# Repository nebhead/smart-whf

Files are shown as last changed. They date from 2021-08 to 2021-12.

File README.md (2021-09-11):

# Smart Whole House Fan

## ESP8266 Based Whole House Fan Controller / Timer

This is a _smarter_ whole house fan controller that can be controlled via a Web UI, and sports a nice OLED screen for status while operating.

**Warning:** It should not go without saying that working with high voltage power is extremely dangerous and should be attempted only by experienced/qualified persons.  This project is provided as-is, with no warranty, gaurentees of fitness, and disclaims all potential damages.  The developer assumes no liability for damage, injury or death that might result from using this.  Implement at your own risk.  

__Features:__

* Web UI for controlling speed and setting timer
* OLED Screen displays operation and timer
* Physical buttons to adjust speed and timer
* Physical button LOCK to prevent kids, accidental or curious button pushers from starting up the fan when you don't want them to
* REST API for controlling the fan via an application (no API key)
* MQTT support for Home Assistant (this needs some help, but the basics work)
* 3D Printable Faceplates / Buttons for mounting

__Pictures:__

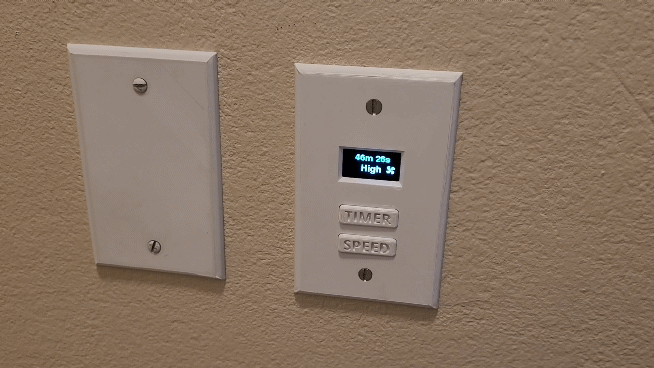
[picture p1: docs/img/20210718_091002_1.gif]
The Finished Product

The final product.  

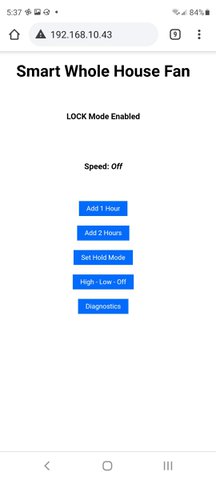
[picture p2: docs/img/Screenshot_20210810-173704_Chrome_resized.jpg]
Chrome

Chrome Screenshot on a mobile device.

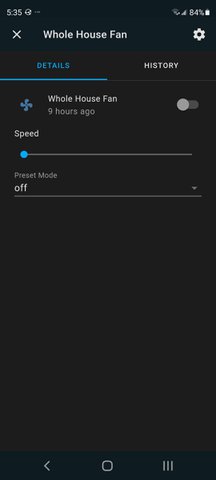
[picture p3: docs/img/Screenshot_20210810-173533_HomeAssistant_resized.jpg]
Home Assistant

Home Assistant Screenshot on a mobile device.

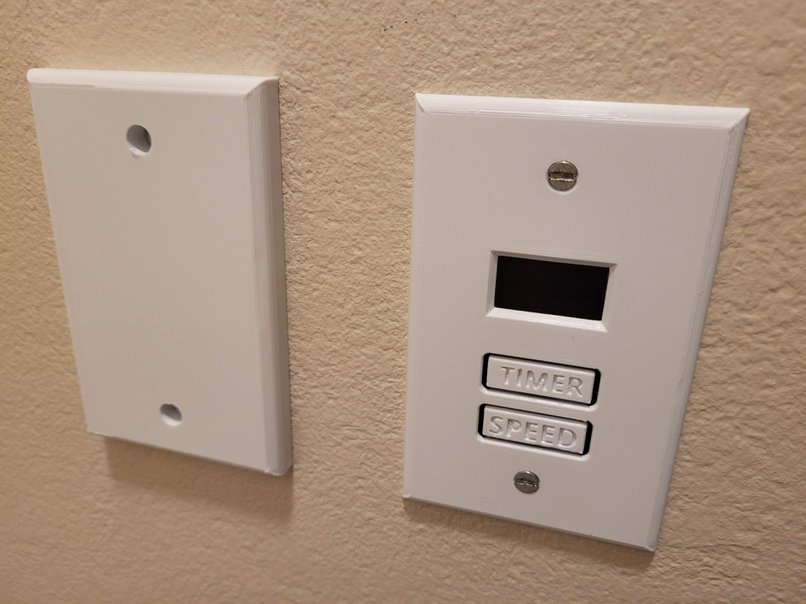
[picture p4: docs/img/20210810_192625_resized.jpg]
Off State

This is the final 3D Printed design with integrated buttons on the control side and a thicker wall plate on the relay side (for more space).

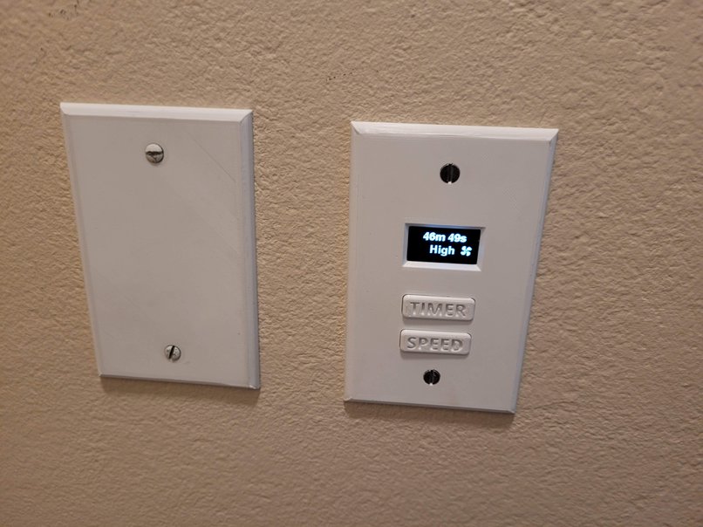
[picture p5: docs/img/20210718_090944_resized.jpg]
On State

This is the original 3D printed design, with large free-floating buttons.  But this give you a better idea of what the display looks like. 

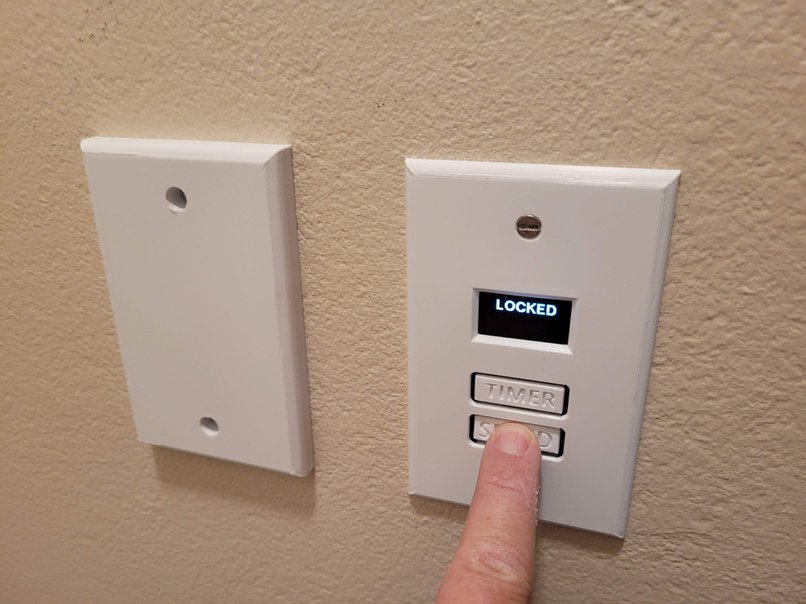
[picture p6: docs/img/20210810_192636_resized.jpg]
LOCKED

Example of what happens when the physical buttons are locked out and someone presses a button.  

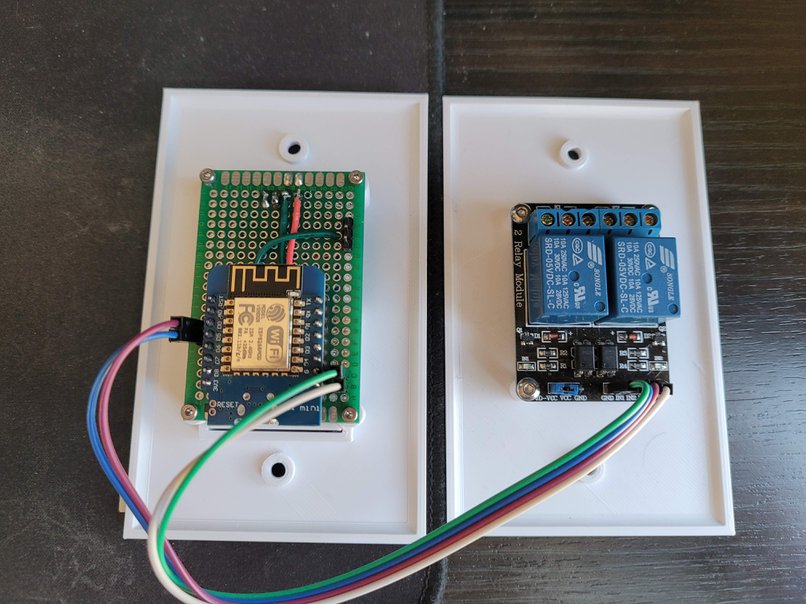
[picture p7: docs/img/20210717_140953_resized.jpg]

An example of how I mounted the perfboard to the backside of the outlet faceplate.  Also the relay mounted to the back of the faceplate.  In retrospect, it might be good to mount the relay up higher so that it has space for the wiring coming out of the bottom.  

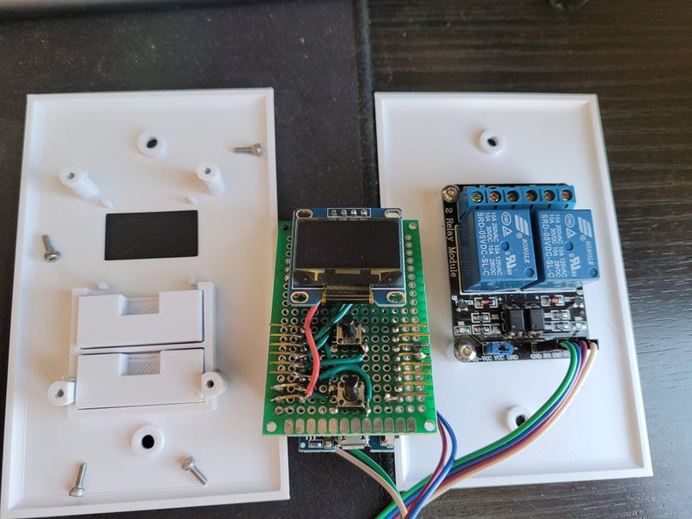
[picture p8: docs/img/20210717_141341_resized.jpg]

Front side of the perfboard wiring, with tack switches, and OLED display.  Note I used some taller tack switches, but you could modify the buttons ont he 3D print to go lower if you want.  

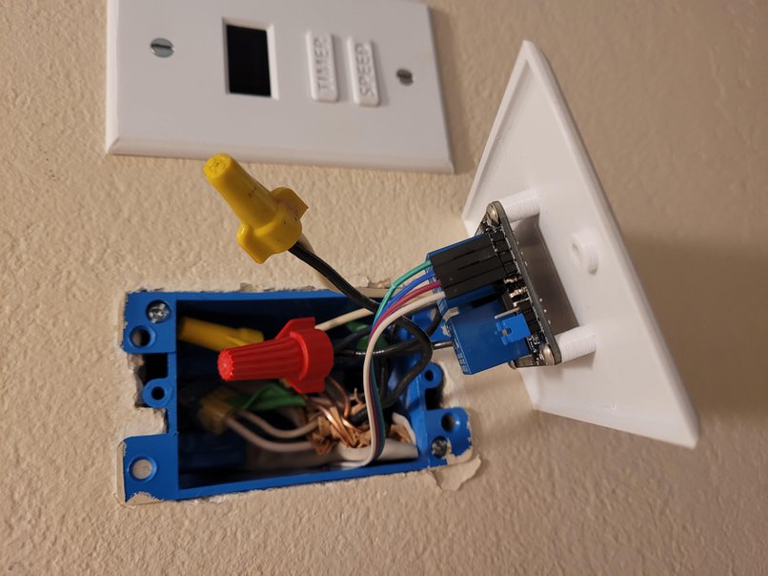
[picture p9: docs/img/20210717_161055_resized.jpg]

AHhh! Not enough space for the relay to tuck up into this outlet.  I ended up switching to smaller wire nuts and 18 AWG wire for the connections to the relay AND thickened the 3D printed wall plate so that it could all fit.  

### The Parts List

* **ESP8266 Board** - I used a Wemos D1 Mini due to it's small form factor, but many other variants of ESP8266 boards could be used as well.  I ordered [these D1 Mini boards](https://www.amazon.com/gp/product/B081PX9YFV) from Amazon, which are great because they come with lots of header options that you can choose from.  This made it easy for me to use a longer pin female headers to stick through the perfboard and to use to make connections to the other components.   
* **2-Channel Relay** - Used to control power to High / Low speeds. Using the mechanical relays, as they seem to have a higher current rating.  [Amazon Link](https://www.amazon.com/SainSmart-101-70-100-2-Channel-Relay-Module/dp/B0057OC6D8)
* **120V AC Power Supply to 5V DC** - Got this incredibly tiny supply from Amazon that can fit in the enclosure.  It's amazing.  [Amazon Link](https://www.amazon.com/gp/product/B08ZSW2PP8)
* **Dupont Cables** - Female to Female for connecting your GPIOs to the relay board. Readily found on Amazon, etc.  
* **SSD1306 OLED Display** - Cheap and commonly found OLED display. This is not the specific one I used, but here is a similar verson on [Amazon](https://www.amazon.com/128X64-Display-SSD1306-Arduino-Raspberry/dp/B085WCRS7C). 
* **Tactile Switches** - I purchased a bunch of sizes of tactile switches and just used the 8 or 9mm sizes for my project, but your mileage may vary. [Amazon Link](https://www.amazon.com/gp/product/B071KX71SV)
* **Project Board** - I utilized some standard 4cm x 6cm project board for this project, but you could choose to utilize other sizes.  [Amazon Link](https://www.amazon.com/gp/product/B00NQ37V0K)
* **2.54pitch headers** - As with the dupont cables, these can be readily found almost anywhere, including Amazon.
* **220V 5A Slow Blow Fuses & Fuse Holders** - To add some protection to your home, I highly recommend using a fuse to this build so that if a short occurs, it will hopefully blow the fuse and prevent an electrical fire.  [Amazon Link to Fuse Assortment](https://www.amazon.com/gp/product/B08QCDHPCJ/),  [Amazon Link to Fuse Holder](https://www.amazon.com/DIGITEN-5x20mm-Holder-Inline-screw/dp/B00VLBAF84/)

### Default GPIO Mapping
+ GPIO 0 - Add Time Button
+ GPIO 2 - Cycle Speed Button (High, Low, Off)
+ GPIO 14 - Relay for HIGH speed
+ GPIO 16 - Relay for LOW speed 

### Schematics

Basic Wiring Schematic for the entire project.  This was built for my home system and yours may vary.  Please build this at your own risk.  The developer takes no responsibility for destroyed equipment, house fires, electric shock.  Please do not attempt unless you are confident you know what you are doing.  

__Low Voltage Schematic:__
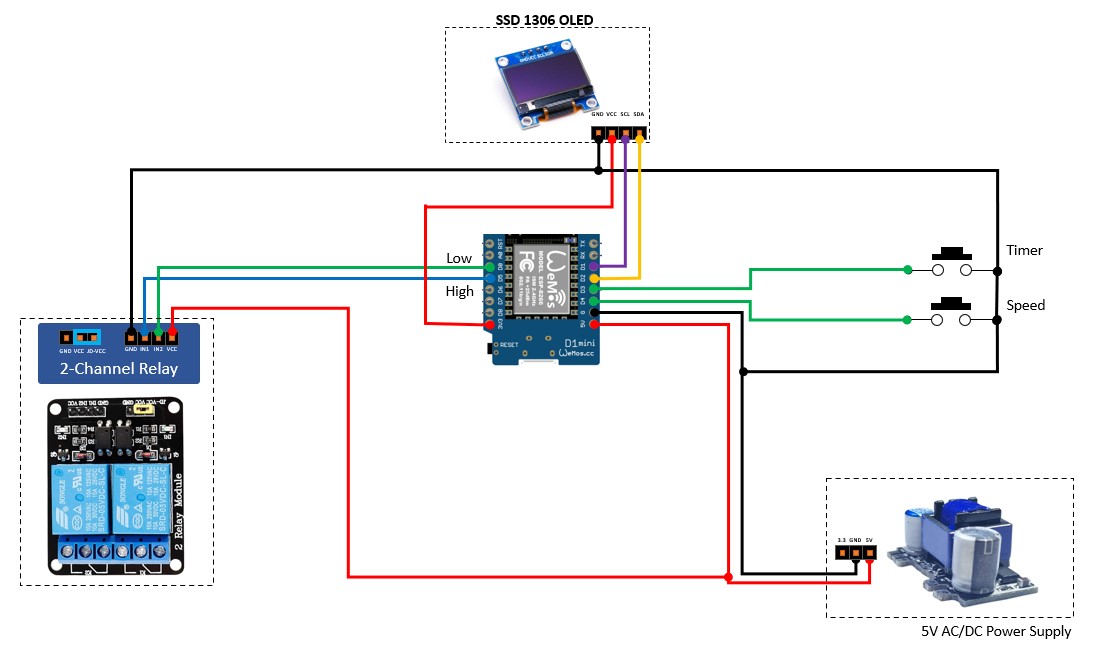
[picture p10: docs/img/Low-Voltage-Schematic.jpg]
Low Voltage Schematic


__High Voltage Schematic:__
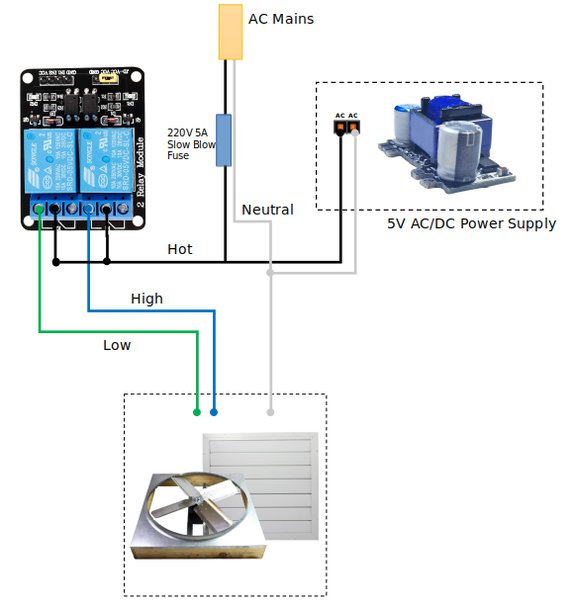
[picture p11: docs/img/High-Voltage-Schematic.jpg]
High Voltage Schematic


### HW Install

Standard whole house fan systems generally have two speeds that are selected by applying power to either the high speed circuit or the low speed circuit.  In the reference schematic above, we show that the relays are acting as the selector for the hot (black) wire, feeding AC current to the fan.  The nuetral should be wired together with a wirenut (or other terminal).  

I personally ended up using 18 guage wire for the connections to the relay due to the challenges of the tight space in my wall box.  However, you may want to check the wiring requirements for your whole house fan, to ensure you are using the minimum gauge wire.  

Also the power supply that I selected, simply needs mains hot and nuetral connected.  On this side, I used 18 gauge wire, simply because this is what I had, and it should be safe give the small amount of power this supply is using.  

## Software Installation

 ##### To install the ESP8266 board, (using Arduino 1.6.4+):
  - Add the following 3rd party board manager under "File -> Preferences -> Additional Boards Manager URLs":
       http://arduino.esp8266.com/stable/package_esp8266com_index.json
  - Open the "Tools -> Board -> Board Manager" and click install for the ESP8266"
  - Select your ESP8266 in "Tools -> Board"

 ##### Library Dependancies include:
   - WiFiManager (by TZAPU) (https://github.com/tzapu/WiFiManager)
   - Adafruit SSD1306 for the OLED display
   - Adafruit GFX library for graphics manipulations / fonts 
   - ArduinoJSON for parsing API inputs / outputs
   - PubSubClient for MQTT Capabilities

  To install the libraries, go to the libraries manager in the Arduino IDE (Tools -> Manage Libraries).  Search for the libraries listed above and install each.  

 ##### MQTT Settings

  Make sure that the following line in smart-whf.ino is not commented out:

  ```
  #define mqttenabled // Comment out this line to disable MQTT support
  ```
  
  In the smart-whf.ino file, modify your MQTT settings for your setup, if using the MQTT feature.  The WifiManager has all of these settings included, however, if you can pre-populate these, it makes setup just a little faster.  

```  
// Edit these values for your implementation
char defaultmqttServer[] = "192.168.10.46";  // put your MQTT Server Address here
char defaultmqttPort[] = "1883"; // put your MQTT Server Port here
char defaultmqttUser[] = "mqtt-user"; // put your MQTT Server Username here
char defaultmqttPassword[] = "password"; // put your MQTT Server Password here
// End value edit
```

 ##### Configure Home Assistant

   First you'll need to ensure that MQTT Broker has been installed from the add-on store.  This is out of scope of this guide, but it's likley that you already have this installed if you are reading this.  Then, modify the `configuration.yaml` file by adding the below:

```
# Configuration for the whole house fan in Home Assistant
# The below goes into your configuration.yaml file

fan whft:
- platform: mqtt
  name: "Whole House Fan"
  icon: "mdi:fan"
  state_topic: "whfan/on/state"
  command_topic: "whfan/on/set"
  percentage_state_topic: "whfan/percentage/state"
  percentage_command_topic: "whfan/percentage/set"
  preset_mode_command_topic: "whfan/preset/set"
  preset_mode_state_topic: "whfan/preset/state"
  preset_modes:
  - "timer"
  - "hold"
  - "off"
  payload_on: "ON"
  payload_off: "OFF"
  speed_range_min: 1
  speed_range_max: 2
  qos: 0  
```

Restart Home Assistant and you should be able to add the Smart Whole House Fan entity to your UI.  

__NOTE:__ I could _really_ use some help from anyone who has experience with Home Assistant to improve this configuration and MQTT support.  For example, being able to add time to the timer from the Home Assistant UI would be awesome.  This is an area I just haven't had time to mess with. 

 ##### Initial Wifi Setup: 
  - To connect your device to WiFi, use a smartphone or computer with WiFi to connect to the board AP (SSID: Smart-WHF-AP).
  - Then open a broswer and navigate to __192.168.4.1__ to configure the device for WiFi.
  - Optionally configure MQTT settings, if you have it built in.  
  - Once configured for your wifi network, you should be all set. 

 ### 3D Printed Parts

 You'll find STL's for 3D Printing your own faceplates in the `/assets/stl/` folder.  

 All STL files were created using OnShape which is free for personal use.  The original design files are located [here](https://cad.onshape.com/documents/4ed1076b86430447dbe85914/w/bb85ae4fb526a0970ad92e38/e/43ed86bf169133e95db9fccc) so that you can copy, export, and make your own tweaks to fit your needs.  

 There are a few options to choose from.  

- __Two single-gang outlet boxes:__ 
  * __Control-Face-Plate.stl:__ Standard Control Face Plate, without buttons.  In this configuration, you'll need to print the __SpeedButtonTall.stl__ and the __TimeButton-Tall.stl__ which can be assembled later.  I found this version to be a little finicky with button presses, but your mileage may vary.  All should print in place with no supports. 
  * __Control-Face-Plate-Int-Buttons.stl:__ This is the same Control Face Plate as above, but with integrated buttons.  This should print in place, with no supports.  I found this version to be much more reliable with button presses, giving a satisfying click on each button press.  It's not as aesthetically pleasing as the above, but it is more functional.
  * __Relay-Face-Plate.stl:__ Standard thickness faceplate for mounting the relay module to.  Prints in place with no supports.  
  * __Relay-Face-Thicc.stl:__ A thicker relay face plate to accomodate space for the relay module and the bulk of wiring inside the outlet box.  I eventually settled on this solution due to the amount of wiring in my installation.  Prints in place with no supports. 

- __One dual-gang outlet box:__
  * __Dual-Gang-Face-Full.stl:__ This is a single faceplate with mounting for both the relay module and the control board w/OLED screen.  Buttons are integrated, as I feel this is a much better button solution.  

- __Power Supply Box (optional):__
  * __PowerSupplyBase - PSBase.stl:__ This is the optional base for the above linked power supply.  I wanted to enclose the power-supply to ensure that there were no shorts if any of the mains wires (or ground) was accidentally touching.  Print in place, no supports. 
  * __PowerSupplyLid - PSLid.stl:__ The lid for the power-supply box.  Print in place, no supports. 

Mounting hardware for the boards are simple M3x8mm (or M3x5mm) bolts.  

### Usage

There are effectively four different ways to use the Smart Whole House fan.  

__1. Physical Buttons__

The physical buttons on the front are fairly simple to use.  

The "Timer" button will set the timer in the following increments when pressed: 1h, 2h, 3h, 4h, 6h, 8h, 10h, HOLD (hold will keep the fan on indefinitely).  

The "Speed" button will cycle through speed settings when pressed: High -> Low -> Off

Pressing the Speed button when the fan is OFF, will set the timer to the default time of 1h automatically.  However, pressing the Timer button when the fan is off, will not select the speed.  

Pressing the Speed button and the Timer button at the _same_ time will briefly display the WiFi SSID and the IP Address of the device.  This might be helpful if you are trying to connect to the web interface and forgot the IP.  

Pressing the Speed button and the Timer button at the _same_ time for six seconds will __LOCK__ the physical buttons.  If the buttons are pressed after LOCK mode is enabled, then the screen will display "LOCKED".  Pressing the Speed button and the Timer button at the _same_ time for three more seconds will __UNLOCK__ the physical buttons.  __Note:__ Locking from the physical buttons will cancel the timer and turn off the fan, if it was already running.  Turning on the fan from the WebUI, MQTT, or API will disable lock mode as a safety mechanism, so you always have the ability to turn off from physical buttons while the fan is running. 

__2. WebUI__

The WebUI can be accessed from any browser by going to the IP address of the device.  There is a menu of buttons, similar to the physical buttons, but slightly different.  

* __Add 1 Hour__ - This allows you to add an hour to the timer. 
* __Add 2 Hours__ - This allows you to add two hours to the timer.
* __Set Hold Mode__ - This will enter hold mode, and the fan will be active until turned off. 
* __High - Low - Off__ - Similar to the physical button for speed, this will cycle through High -> Low -> Off modes.  
* __Diagnositcs__ - This will take you to some additional information about the WiFi Network, MQTT Status, and will allow you to __RESTART__ the device, or to __LOCK/UNLOCK__ the physical buttons.  

__3. MQTT w/HomeAssistant__

As described in the Home Assistant section above, the MQTT interface can be used to control the fan.  This means that the whole house fan can even be controlled via your Google Home or Amazon Alexa enabled devices.  The interface in Home Assistant is pretty basic (on/off), set fan speed low/high/off, and set the preset mode to timer/hold/off.  Admittedly, this is my first project using MQTT and Home Assistant, so feedback on how to improve this is very welcome.  

__4. REST API__

Last but not least, there is a basic REST API that can be utilized to control the fan functions as well.  

A GET request to http://whf.device.ip.address/api will return the following if the fan is off: 

```
{"power":"off","speed":"off"}
```

If the fan is running, it will return something like this: 

```
{"power":"on","speed":"low","holdmode":false,"timer":"59m 46s"}
```

A POST request to http://whf.device.ip.address/api should contain commands in the following JSON format: 

```
    {
      "power" : "on", "off"           # Turn on or off
      "speed" : "high", "low", "off"  # Can be high, low or off
      "holdmode" : True, False        # Can be True or False
      "addtime" : 1,2                 # Add hours can be 1 or 2
    }
```

On a POST request, the fan will return the same JSON output as above if running or off.  

### Credits

Created by Ben Parmeter. Check out my other projects on [github](https://github.com/nebhead). If you enjoy this software and feel the need to donate a cup of coffee, a frosty beer or a bottle of wine to the developer you can click [here](https://paypal.me/benparmeter).

Of course, none of this project would be available without the wonderful and amazing folks below.  If I forgot anyone please don't hesitate to let me know.  

* **Adafruit** - for the SSD1306 and Graphics Libraries.  
* **WiFiManager** - by TZAPU [github](https://github.com/tzapu/WiFiManager)
* **ArduinoJSON** - by Benoît Blanchon for making parsing inputs/outputs of the API easier [arduinojson.org](https://arduinojson.org/)
* **PubSubClient** - by Nick O'Leary for adding the MQTT capabilities to the fan [github.com](https://github.com/knolleary/pubsubclient)

### Licensing

This project is licensed under the MIT license.

```
MIT License

Copyright (c) 2021 Ben Parmeter

Permission is hereby granted, free of charge, to any person obtaining a copy
of this software and associated documentation files (the "Software"), to deal
in the Software without restriction, including without limitation the rights
to use, copy, modify, merge, publish, distribute, sublicense, and/or sell
copies of the Software, and to permit persons to whom the Software is
furnished to do so, subject to the following conditions:

The above copyright notice and this permission notice shall be included in all
copies or substantial portions of the Software.

THE SOFTWARE IS PROVIDED "AS IS", WITHOUT WARRANTY OF ANY KIND, EXPRESS OR
IMPLIED, INCLUDING BUT NOT LIMITED TO THE WARRANTIES OF MERCHANTABILITY,
FITNESS FOR A PARTICULAR PURPOSE AND NONINFRINGEMENT. IN NO EVENT SHALL THE
AUTHORS OR COPYRIGHT HOLDERS BE LIABLE FOR ANY CLAIM, DAMAGES OR OTHER
LIABILITY, WHETHER IN AN ACTION OF CONTRACT, TORT OR OTHERWISE, ARISING FROM,
OUT OF OR IN CONNECTION WITH THE SOFTWARE OR THE USE OR OTHER DEALINGS IN THE
SOFTWARE.
```

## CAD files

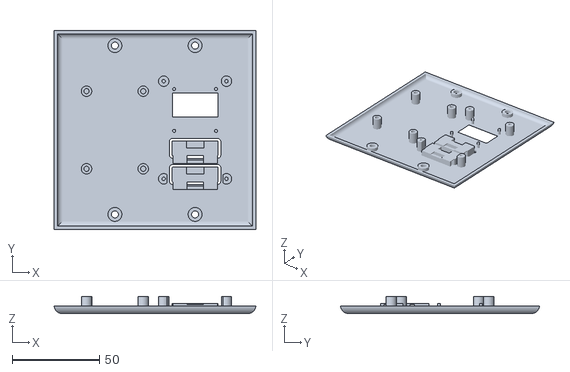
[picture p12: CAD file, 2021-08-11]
assets/stl/Dual-Gang-Face-Full.stl
115.8 x 114.2 x 10.0

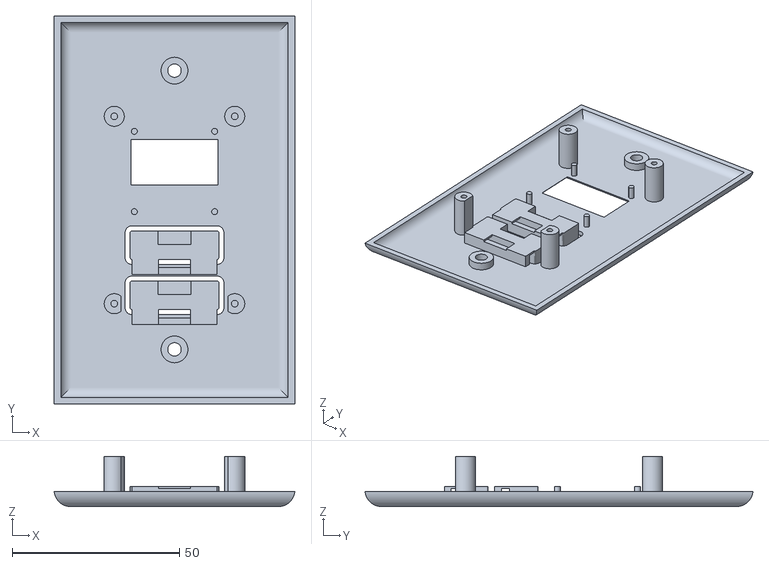
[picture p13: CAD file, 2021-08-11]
assets/stl/Control-Face-Plate-Int-Buttons.stl
71.9 x 115.9 x 15.0

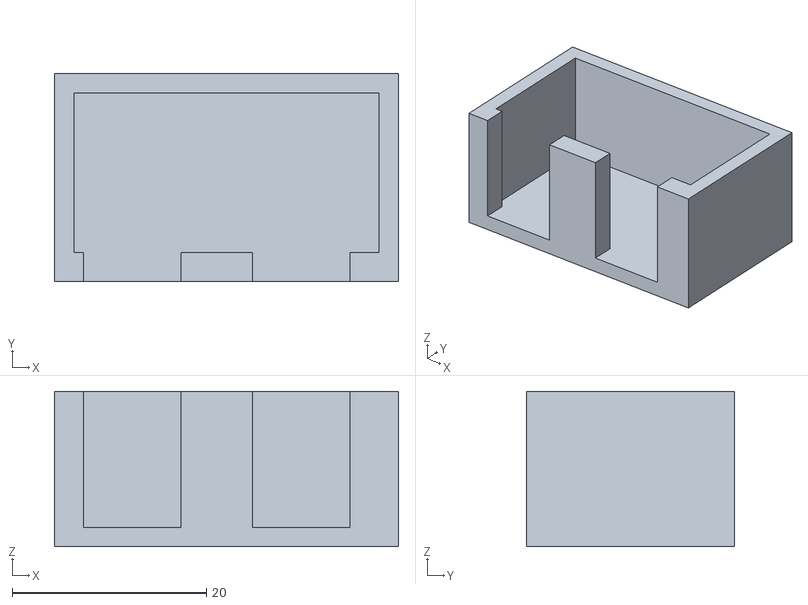
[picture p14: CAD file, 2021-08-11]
assets/stl/PowerSupplyBase - PSBase.stl
35.4 x 21.4 x 16.0

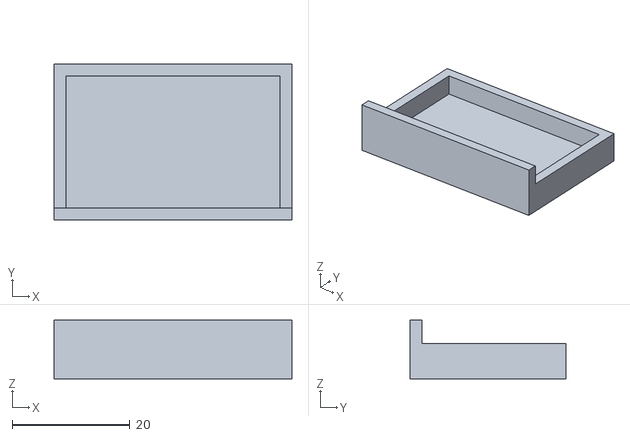
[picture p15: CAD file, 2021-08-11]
assets/stl/PowerSupplyLid - PSLid.stl
40.4 x 26.4 x 10.0

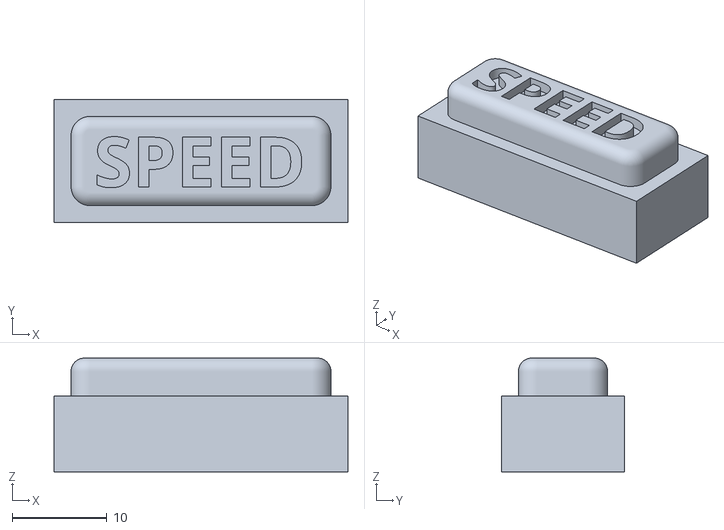
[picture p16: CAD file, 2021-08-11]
assets/stl/SpeedButtonTall.stl
31.0 x 13.0 x 12.0

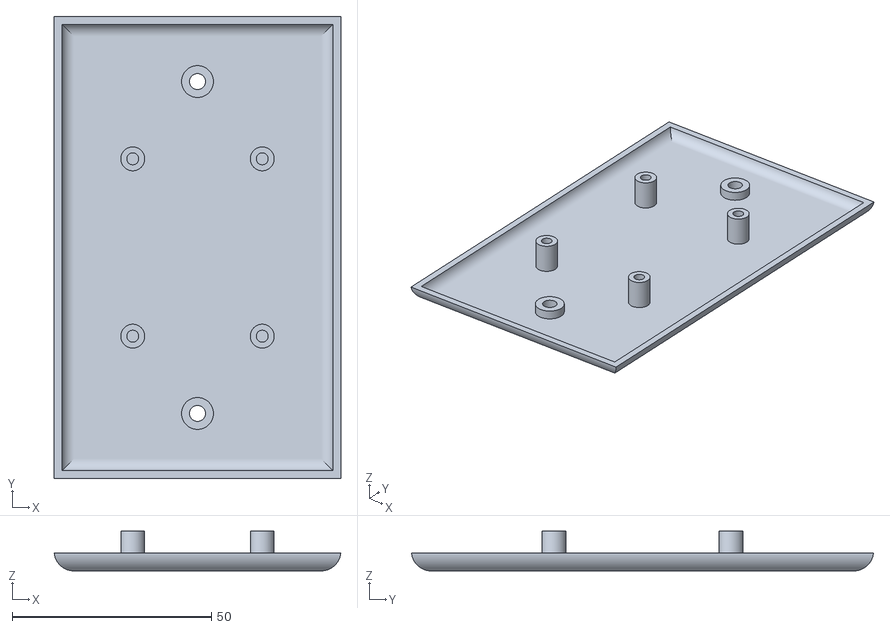
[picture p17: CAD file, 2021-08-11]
assets/stl/Relay-Face-Plate.stl
71.9 x 115.9 x 10.0

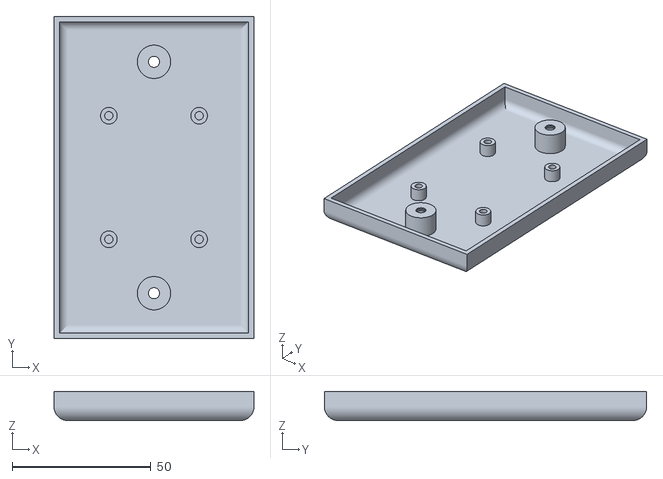
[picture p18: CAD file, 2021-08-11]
assets/stl/Relay-Face-Thicc.stl
72.0 x 116.0 x 10.5

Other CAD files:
assets/stl/TimeButton-Tall.stl
assets/stl/Control-Face-Plate.stl

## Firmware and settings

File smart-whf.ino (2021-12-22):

/*
 Simple Smart Whole House Fan Timer Controller

 Controlled via physical buttons or web user interface. 

 Designed for ESP8266 based boards like the Wemos D1 Mini or NodeMCU
 
 To install the ESP8266 board, (using Arduino 1.6.4+):
  - Add the following 3rd party board manager under "File -> Preferences -> Additional Boards Manager URLs":
       http://arduino.esp8266.com/stable/package_esp8266com_index.json
  - Open the "Tools -> Board -> Board Manager" and click install for the ESP8266"
  - Select your ESP8266 in "Tools -> Board"

 Dependancies include:
   - WiFiManager (by TZAPU) (https://github.com/tzapu/WiFiManager)
   - Adafruit SSD1306 for the OLED display
   - Adafruit GFX library for graphics manipulations / fonts 
   - ArduinoJSON for parsing API inputs / outputs
   - PubSubClient for MQTT Capabilities

 Initial Wifi Setup: 
  To connect your device to WiFi, use a smartphone or computer with WiFi to connect to the board AP (SSID: Smart-WHF-AP).
  Then open a broswer and navigate to 192.168.4.1 to configure the device for WiFi. 
*/

#define mqttenabled // Comment out this line to disable MQTT support
#include <FS.h> // Apparently need this to be included first
#include <ESP8266WiFi.h>
#include <WiFiClient.h>
#include <ESP8266mDNS.h>
#include <ESP8266WebServer.h>   // Include the WebServer library
#include <WiFiManager.h> 
#include <SPI.h>
#include <Wire.h>
#include <Adafruit_GFX.h>
#include <Adafruit_SSD1306.h>
#include <Fonts/FreeSansBold12pt7b.h>
#include <ArduinoJson.h>
#include <WiFiUdp.h>
#include <ArduinoOTA.h>

#ifdef mqttenabled
// If MQTT enabled, then setup mqtt
#include <PubSubClient.h>

// Edit these values for your implementation
char defaultmqttServer[] = "192.168.10.242";  // put your MQTT Server Address here
char defaultmqttPort[] = "1883"; // put your MQTT Server Port here
char defaultmqttUser[] = "mqtt-user"; // put your MQTT Server Username here
char defaultmqttPassword[] = "password"; // put your MQTT Server Password here
int mqttRetries = 100; // number of retries before disabling MQTT, if connection fails
// End value edit
String mqttServer = String(defaultmqttServer);
int mqttPort = atoi(defaultmqttPort);
String mqttUser = String(defaultmqttUser);
String mqttPassword = String(defaultmqttPassword);
const char* mqttCommandTopic = "whfan/on/set";
const char* mqttPresetCommandTopic = "whfan/preset/set";
const char* mqttPresetStateTopic = "whfan/preset/state";
const char* mqttStateTopic = "whfan/on/state";
const char* mqttAvailTopic = "whfan/on/avail";
const char* mqttSpeedStateTopic = "whfan/speed/state";
const char* mqttSpeedCommandTopic = "whfan/speed/set";
const char* mqttPercentageStateTopic = "whfan/percentage/state";
const char* mqttPercentageCommandTopic = "whfan/percentage/set";
unsigned long mqttLastCheck; 
WiFiClient espClient;
PubSubClient client(espClient);
#endif 

const char* wifiHostname = "whfan";
ESP8266WebServer server(80);    // Create a webserver object that listens for HTTP request on port 80

#define SCREEN_WIDTH 128 // OLED display width, in pixels
#define SCREEN_HEIGHT 64 // OLED display height, in pixels

// Declaration for an SSD1306 display connected to I2C (SDA, SCL pins)
// The pins for I2C are defined by the Wire-library. 
// On an arduino UNO:       A4(SDA), A5(SCL)
// On an arduino MEGA 2560: 20(SDA), 21(SCL)
// On an arduino LEONARDO:   2(SDA),  3(SCL), ...
#define OLED_RESET     -1 // Reset pin # (or -1 if sharing Arduino reset pin)
#define SCREEN_ADDRESS 0x3C ///< See datasheet for Address; 0x3D for 128x64, 0x3C for 128x32
Adafruit_SSD1306 display(SCREEN_WIDTH, SCREEN_HEIGHT, &Wire, OLED_RESET);

#define DEBOUNCE 250 // Millisecond debounce for buttons
#define REFRESH 200 // Millisecond refresh for display 
#define GPIO_timebtn 0 // Input button for time selection
#define GPIO_speedbtn 2 // Input button for speed selection
#define GPIO_HIGHrelay 14 // High Fan Speed Relay Output Enable
#define GPIO_LOWrelay 16 // Low Fan Speed Relay Output Enable

int state = 0;  // Current Fan Speed / State : 0 = Off, 1 = High, 2 = Low
int iconstate = 0;  // Current Icon Animation Image : 0 = Starting Position, 1-2 = 22.5d rotated, 3-4 = 45d rotated, 5-6 = 67.5d rotated
bool holdmode = false; // Indicates hold mode
bool lockmode = false; // Indicates lock mode (physical buttons are locked)
bool lockinitiated = false;  // Indicates unlock / lock mode has been initiated
unsigned long locktimer = 0; // Tracks start time of lock / unlock events
unsigned long start_time = 0;   // Track start time of the fan
unsigned long runtime = 0;  // Track total runtime
unsigned long timebtnlastpress = 0;  // Millis when the time button was last pressed, for debounce
unsigned long spdbtnlastpress = 0;  // Millis when the speed button was last pressed, for debounce
unsigned long displayrefreshlast = 0;  // Millis when the screen was last refreshed
unsigned long now = 0; // Tracks the current millis output

String timestring = "";  // Time String to display

String favicon = "<link rel=\"shortcut icon\" href=\"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" />";

// Fan Icon Animation - 24x24 ICON rotates 22.5 degrees per step
const unsigned char fanicon0 [] PROGMEM = {
  0x00, 0x3e, 0x00, 0x00, 0x7f, 0x80, 0x00, 0xff, 0x80, 0x00, 0xff, 0x80, 0x00, 0xff, 0x80, 0x00, 
  0xff, 0x00, 0x00, 0x7e, 0x00, 0x78, 0x7c, 0x00, 0x7c, 0x3c, 0x38, 0xfe, 0x66, 0xfe, 0xff, 0xd3, 
  0xfe, 0xff, 0xb9, 0xff, 0xff, 0x99, 0xff, 0xff, 0xc3, 0xff, 0x7f, 0x64, 0x7f, 0x1c, 0x3c, 0x3e, 
  0x00, 0x3e, 0x1e, 0x00, 0x7e, 0x00, 0x00, 0xff, 0x00, 0x01, 0xff, 0x00, 0x01, 0xff, 0x00, 0x01, 
  0xfe, 0x00, 0x01, 0xfe, 0x00, 0x00, 0x78, 0x00
};

const unsigned char fanicon1 [] PROGMEM = {
  0x00, 0xf0, 0x00, 0x01, 0xf8, 0x00, 0x03, 0xfc, 0x00, 0x07, 0xf8, 0x00, 0x07, 0xf8, 0x00, 0x07, 
  0xf8, 0x38, 0x03, 0xf0, 0xfc, 0x03, 0xf1, 0xfe, 0x01, 0xfb, 0xff, 0x00, 0xc7, 0xff, 0x30, 0x5b, 
  0xff, 0xfc, 0xb9, 0xff, 0xff, 0xb9, 0x3e, 0xff, 0xc2, 0x04, 0xff, 0xe7, 0x00, 0xff, 0x9f, 0x80, 
  0x7f, 0x8f, 0xc0, 0x3f, 0x0f, 0xc0, 0x1c, 0x1f, 0xe0, 0x00, 0x1f, 0xe0, 0x00, 0x3f, 0xe0, 0x00, 
  0x3f, 0xc0, 0x00, 0x1f, 0x80, 0x00, 0x0e, 0x00
};

const unsigned char fanicon2 [] PROGMEM = {
  0x00, 0x00, 0x00, 0x03, 0x80, 0x00, 0x0f, 0xc0, 0x40, 0x1f, 0xc1, 0xf0, 0x1f, 0xc3, 0xf8, 0x1f, 
  0xc7, 0xfc, 0x3f, 0xc7, 0xfe, 0x1f, 0xc7, 0xfe, 0x1f, 0xff, 0xfc, 0x0f, 0xc7, 0xfc, 0x03, 0x9b, 
  0x00, 0x00, 0xb8, 0x00, 0x00, 0xb9, 0x00, 0x01, 0xc3, 0xc0, 0x3f, 0xe7, 0xf0, 0x7f, 0xff, 0xf8, 
  0x7f, 0xe3, 0xf8, 0x7f, 0xe3, 0xf8, 0x3f, 0xc3, 0xf8, 0x1f, 0xc3, 0xf8, 0x0f, 0x83, 0xf0, 0x00, 
  0x03, 0xe0, 0x00, 0x01, 0x80, 0x00, 0x00, 0x00
};

const unsigned char fanicon3 [] PROGMEM = {
  0x00, 0x00, 0x00, 0x00, 0x07, 0xc0, 0x00, 0x0f, 0xe0, 0x08, 0x1f, 0xf0, 0x3e, 0x1f, 0xf0, 0x3e, 
  0x1f, 0xf0, 0x7f, 0x1f, 0xf0, 0x7f, 0x1f, 0xc0, 0x7f, 0x9f, 0x00, 0x7f, 0xc6, 0x00, 0x7f, 0x9a, 
  0x00, 0x3f, 0xb9, 0xf8, 0x0f, 0xb9, 0xfc, 0x00, 0x43, 0xfe, 0x00, 0x67, 0xfe, 0x00, 0xf9, 0xfe, 
  0x03, 0xf8, 0xfe, 0x0f, 0xf8, 0xfe, 0x1f, 0xf8, 0x7c, 0x1f, 0xf8, 0x78, 0x0f, 0xf0, 0x00, 0x07, 
  0xf0, 0x00, 0x03, 0xe0, 0x00, 0x00, 0x00, 0x00
};

void handleRoot(); // function prototypes for HTTP handlers
void handleNotFound();  // 404 not found
void handleAPI();     // function for handling API call
void handleAddTime1();   // function for adding 1 hour to time
void handleAddTime2();   // function for adding 2 hours to time
void handleHoldMode();   // function for setting HOLD mode
void handleChangeSpeed();  // function to change fan speed High - Low - Off 
void handleRefreshData();  // function to handle refresh data for main page
void handleDiag(); // function for display diagnostic screen
void handleRestart(); // function for restarting the ESP
void handleWificonfig(); // function to reset connection data and start AP mode
void handleToggleLock(); // function to toggle lock mode 

// **** Init Wifi / Wifi Manager
WiFiManager wifiManager;

// Flag for saving MQTT data to config.json
bool shouldSaveConfig = false;

// Callback notifying us of the need to save config.json
void saveConfigCallback () {
  Serial.println("Intent to Save Config.");
  shouldSaveConfig = true;
}

// This function's author is apicquot from https://forum.arduino.cc/index.php?topic=228884.0
String IpAddress2String(const IPAddress& ipAddress)
{
    return String(ipAddress[0]) + String(".") +
           String(ipAddress[1]) + String(".") +
           String(ipAddress[2]) + String(".") +
           String(ipAddress[3]);
}

void setup(void){
  String event;
  Serial.begin(115200); // Start the Serial communication to send messages to the computer
  // Setup GPIO Pins
  pinMode(GPIO_timebtn, INPUT_PULLUP);     // Input for button 1  (timebtn)
  pinMode(GPIO_speedbtn, INPUT_PULLUP);     // Input for button 2  (speedbtn)
  pinMode(GPIO_HIGHrelay, OUTPUT);  // Output for HIGH relay
  pinMode(GPIO_LOWrelay, OUTPUT);  // Output for LOW relay

  digitalWrite(GPIO_HIGHrelay, HIGH);  // Turn OFF HIGH relay
  digitalWrite(GPIO_LOWrelay, HIGH);  // Turn OFF LOW relay

  delay(10);
  Serial.println('\n');

  // **** Init Display
  // SSD1306_SWITCHCAPVCC = generate display voltage from 3.3V internally
  if(!display.begin(SSD1306_SWITCHCAPVCC, SCREEN_ADDRESS)) {
    Serial.println(F("SSD1306 allocation failed"));
    for(;;); // Don't proceed, loop forever
  }

  // Show initial display buffer contents on the screen --
  // the library initializes this with an Adafruit splash screen.
  display.clearDisplay();
  display.display();

  display.setFont();
  display.setTextSize(1);             // Normal 1:1 pixel scale
  display.setTextColor(SSD1306_WHITE);        // Draw white text
  display.setCursor(0,0);
  display.println("Setting Up WiFi...");
  display.setCursor(0,10); 
  display.println("Starting AP Mode...");
  display.display();

  #ifdef mqttenabled
    //read configuration from FS json
  Serial.println("Attempting to Mount Filesystem...");

  if (SPIFFS.begin()) {
    Serial.println("Mounted File System.");
    if (SPIFFS.exists("/config.json")) {
      //file exists, reading and loading
      Serial.println("Looking for config.json File");
      File configFile = SPIFFS.open("/config.json", "r");
      if (configFile) {
        Serial.println("Opened Config File");
        size_t size = configFile.size();
        // Allocate a buffer to store contents of the file.
        std::unique_ptr<char[]> buf(new char[size]);

        configFile.readBytes(buf.get(), size);

#ifdef ARDUINOJSON_VERSION_MAJOR >= 6
        DynamicJsonDocument json(1024);
        auto deserializeError = deserializeJson(json, buf.get());
        serializeJson(json, Serial);
        if ( ! deserializeError ) {
#else
        DynamicJsonBuffer jsonBuffer;
        JsonObject& json = jsonBuffer.parseObject(buf.get());
        json.printTo(Serial);
        if (json.success()) {
#endif
          strcpy(defaultmqttServer, json["mqtt_server"]);
          strcpy(defaultmqttPort, json["mqtt_port"]);
          strcpy(defaultmqttUser, json["mqtt_username"]);
          strcpy(defaultmqttPassword, json["mqtt_password"]);
        } else {
          Serial.println("failed to load json config");
        }
        configFile.close();
      }
    } else {
      Serial.println("File config.json not found.");
    }
  } else {
    Serial.println("Failed to Mount Filesystem");
  }
  //end read
  
  wifiManager.setSaveConfigCallback(saveConfigCallback);

  // Add mqtt server to the WiFi Manager Settings
  // id/name, placeholder/prompt, default, length
  WiFiManagerParameter your_mqtt_server("mserver", "MQTT Server", defaultmqttServer, 40);
  WiFiManagerParameter your_mqtt_port("mport", "MQTT Port", defaultmqttPort, 6);
  WiFiManagerParameter your_mqtt_user("muser", "MQTT Username", defaultmqttUser, 25);
  WiFiManagerParameter your_mqtt_password("mpass", "MQTT Password", defaultmqttPassword, 40);
  
  wifiManager.addParameter(&your_mqtt_server);
  wifiManager.addParameter(&your_mqtt_port);
  wifiManager.addParameter(&your_mqtt_user);
  wifiManager.addParameter(&your_mqtt_password);
  #endif
  
  wifiManager.setHostname(wifiHostname);
  wifiManager.autoConnect("Smart-WHF-AP");

  #ifdef mqttenabled
  // Get values for custom setup
  mqttServer = your_mqtt_server.getValue();
  String mqttPortStrPlaceHolder = your_mqtt_port.getValue();
  mqttPort = mqttPortStrPlaceHolder.toInt();
  mqttUser = your_mqtt_user.getValue();
  mqttPassword = your_mqtt_password.getValue();

  //read updated parameters
  //strcpy(mqttServer, your_mqtt_server.getValue());
  //strcpy(mqttPortStrPlaceHolder, your_mqtt_port.getValue());

  //save the custom parameters to FS
  if (shouldSaveConfig) {
    Serial.println("Saving config.json...");
#ifdef ARDUINOJSON_VERSION_MAJOR >= 6
    DynamicJsonDocument json(1024);
#else
    DynamicJsonBuffer jsonBuffer;
    JsonObject& json = jsonBuffer.createObject();
#endif
    json["mqtt_server"] = mqttServer;
    json["mqtt_port"] = mqttPortStrPlaceHolder;
    json["mqtt_username"] = mqttUser;
    json["mqtt_password"] = mqttPassword;

    File configFile = SPIFFS.open("/config.json", "w");
    if (!configFile) {
      Serial.println("Failed to open config file for writing!!");
    }
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
void loop(void){
  ArduinoOTA.handle();

  server.handleClient();  // Listen for HTTP requests from clients
  
  now = millis();

  #ifdef mqttenabled 
  // Check MQTT Connection (non-blocking)
  if (mqttRetries >= 1) {
    if ((!client.connected()) && (now - mqttLastCheck > 2000)) {
      reconnect();
      mqttLastCheck = now; 
    } else {
      client.loop();
    }
  }
  #endif

  // Get physical input status  
  int timebtn = digitalRead(GPIO_timebtn);
  int speedbtn = digitalRead(GPIO_speedbtn);

  if (lockmode) {
    if ((timebtn == LOW) && (speedbtn == LOW) && (lockinitiated)) {
      // Wait for 3-Seconds to lock
      if ((now - locktimer) > 3000) {
        display.clearDisplay();
        display.setFont(&FreeSansBold12pt7b);
        display.setTextSize(1);             // Normal 1:1 pixel scale
        display.setTextColor(SSD1306_WHITE);        // Draw white text
        display.setCursor(40,20);
        display.println("UN-");
        display.setCursor(15,42);
        display.println("LOCKED");
        display.display();
        delay(2000);
        lockmode = false;
        locktimer = 0;
        lockinitiated = false;
        display.clearDisplay();
        display.display();
      }
    } else if ((timebtn == LOW) && (speedbtn == LOW) && !(lockinitiated)) {
      display.clearDisplay();
      display.setFont(&FreeSansBold12pt7b);
      display.setTextSize(1);             // Normal 1:1 pixel scale
      display.setTextColor(SSD1306_WHITE);        // Draw white text
      display.setCursor(15,20);
      display.println("LOCKED");
      display.setFont();
      display.setTextSize(1);             // Normal 1:1 pixel scale
      display.setCursor(30,50);
      display.println("Hold 3 Sec.");
      display.display();
      locktimer = now;
      lockinitiated = true; // 
    } else if ((timebtn == LOW) || (speedbtn == LOW)) {
      display.clearDisplay();
      display.setFont(&FreeSansBold12pt7b);
      display.setTextSize(1);             // Normal 1:1 pixel scale
      display.setTextColor(SSD1306_WHITE);        // Draw white text
      display.setCursor(15,20);
      display.println("LOCKED");
      display.display();
      delay(1000);
      display.clearDisplay();
      display.display();
      // if both buttons are not pressed, stay in lock mode
      lockinitiated = false; 
      locktimer = 0;
    } else {
      // if both buttons are not pressed, stay in lock mode
      lockinitiated = false; 
      locktimer = 0;
      // DISPLAY STATUS
      displayStatus();
    }
  } else {
    // If both buttons pressed, show status or lock
    if ((timebtn == LOW) && (speedbtn == LOW) && !(lockinitiated) && (locktimer == 0)) {
      locktimer = now;  // Start the lock timer
      Serial.print("Connected to ");
      Serial.println(WiFi.SSID());              // Tell us what network we're connected to
      Serial.print("IP address:\t");
      Serial.println(WiFi.localIP());           // Send the IP address of the ESP8266 to the computer

      display.clearDisplay();
      
      display.setFont();
      display.setTextSize(1);             // Normal 1:1 pixel scale
      display.setTextColor(SSD1306_WHITE);        // Draw white text
      display.setCursor(0,0);
      display.println(WiFi.SSID());
      display.setCursor(0,10); 
      display.println(WiFi.localIP());
      display.display();
    } else if ((timebtn == LOW) && (speedbtn == LOW) && !(lockinitiated) && (now - locktimer > 3000)) {
      lockinitiated = true;
      display.clearDisplay();
      display.setFont(&FreeSansBold12pt7b);
      display.setTextSize(1);             // Normal 1:1 pixel scale
      display.setTextColor(SSD1306_WHITE);        // Draw white text
      display.setCursor(10,20);
      display.println("LOCKING");
      display.display();
    } else if ((timebtn == LOW) && (speedbtn == LOW) && (lockinitiated) && (now - locktimer > 6000)) {
      lockinitiated = false;
      locktimer = 0;
      lockmode = true;
      display.clearDisplay();
      display.setFont(&FreeSansBold12pt7b);
      display.setTextSize(1);             // Normal 1:1 pixel scale
      display.setTextColor(SSD1306_WHITE);        // Draw white text
      display.setCursor(15,20);
      display.println("LOCKED");
      display.display();
      delay(2000);
      setOff();
    } else if ((timebtn == LOW) && (speedbtn == LOW)) {
      // Do nothing
      delay(10);
    } else {
      // Clear lock flags if set (i.e. someone let go of buttons)
      lockinitiated = false; 
      locktimer = 0;

      // DISPLAY STATUS
      displayStatus();

      // If Timer Button pressed:
      if ((timebtn == LOW) && (now - timebtnlastpress > DEBOUNCE)) {
        timebtnlastpress = now; 

        if(runtime < (4 * 60 * 60 * 1000)) {
          addTime(1);  // If less than four hours, add 1 hour to start time)
        } else {
          addTime(2);  // Else add 2 hours to start time)
        }
      }

      // If Speed Button pressed:
      if ((speedbtn == LOW) && (now - spdbtnlastpress > DEBOUNCE))  {
        state += 1;
        spdbtnlastpress = now;

        setSpeed();
      }
    }
  }
  delay (10);
}

void displayStatus() {
  // If display active, display status
  if(((start_time > 0) || (holdmode)) && (now - displayrefreshlast > REFRESH)) {
    displayrefreshlast = now;
    setTimestring();

    display.clearDisplay();
    
    display.setFont(&FreeSansBold12pt7b);
    display.setTextSize(1);             // Normal 1:1 pixel scale
    display.setTextColor(SSD1306_WHITE);        // Draw white text
    display.setCursor(20,20);
    display.println(timestring);

    String statestring = "";
    if (state == 0) {
      statestring = "Off";
      iconstate = 0;
      display.setCursor(40,50);  
    }
    else if (state == 1) {
      statestring = "High";
      iconstate += 2;
      display.setCursor(36,50);  
    }
    else if (state == 2) {
      statestring = "Low";
      iconstate += 1;
      display.setCursor(40,50);  
    }
    display.println(statestring);

    if (iconstate == 0) {
      display.drawBitmap(128-24, 30, fanicon0, 24, 24, 1); 
    }
    else if (iconstate <=2) {
      display.drawBitmap(128-24, 30, fanicon1, 24, 24, 1); 
    }
    else if (iconstate <=4) {
      display.drawBitmap(128-24, 30, fanicon2, 24, 24, 1); 
    }
    else if (iconstate <=6) {
      display.drawBitmap(128-24, 30, fanicon3, 24, 24, 1); 
    }
    else {
      iconstate = 0;
      display.drawBitmap(128-24, 30, fanicon0, 24, 24, 1);
    }
    
    display.display();
  } else if ((start_time > 0) && (!holdmode) && (now - start_time > runtime)) {
    setOff();
  } 
}

void setTimestring() {
  if (holdmode) { 
    timestring = " HOLD ";
  } else if(((millis() - start_time)) < runtime) {
    timestring = "";
    if ((runtime - (millis() - start_time)) < (60 * 60 * 1000)) {  // If less than one hour display mins:secs 
      timestring += ((runtime - (millis() - start_time)) / 60000);
      timestring += "m ";
      timestring += ((runtime - (millis() - start_time)) / 1000) % 60;
      timestring += "s";
    } else if ((runtime - (millis() - start_time)) < (12 * 60 * 60 * 1000)) {  // If less than 10 hours display hours:mins 
      timestring += ((runtime - (millis() - start_time)) % (1000 * 60 * 60 * 24)) / (1000 * 60 * 60);  // Number of hours remaining
      timestring += "h ";
      timestring += ((runtime - (millis() - start_time)) % (1000 * 60 * 60)) / (1000 * 60); // Number of minutes remaining
      timestring += "m ";
    } else {  // Otherwise, show 12h+
      timestring += "12h+";
    }
  }
}
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

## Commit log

2021-08-11 Version 1.0
    This is the first iteration of the Smart(er) Whole House Fan project. This project utilizes the ESP8266 and Arduino libraries to control a whole house fan, via physical buttons, webUI, MQTT or REST A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
    [Control-Face-Plate-Int-Buttons.stl, Control-Face-Plate.stl, Dual-Gang-Face-Full.stl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]
2021-08-11 Fix Low Voltage Schematic
    Whoops, missed a ground connection.
2021-09-10 Added favicon, Updated Documentation
    Added a favicon for the web interface. Should work with most browsers.
    Added recommendation to use fuse on the mains power, to help prevent potential electrical fires, if a short occurs in the power supply or the relays. Updated readme.md and the High Voltage Schematic example.
    [smart-whf.ino]
2021-09-11 Lock Mode Behavior Change
    Turning on the fan from the WebUI, MQTT, or API will disable lock mode as a safety mechanism, so you always have the ability to turn off from physical buttons while the fan is running.
2021-12-22 Graceful MQTT Connection Loss Handling & Added Reset to AP Mode
    Created a variable that tracks the number of connection attempts. If the device fails connect to the MQTT server after this many attempts it will stop checking for MQTT. This should prevent the system from hanging up when the there is no MQTT to connect to.
    Added a button the diagnostics page to reset the wifi connection data and return to AP Mode. This will wipe your credentials and return the device to AP mode. You'll need to log back into the WiFi manager and set your credentials again.
    Known Issue: On reset of the device, the MQTT parameters are lost (and are not pulled from the saved memory). Workaround is to set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
    [smart-whf.ino]
2021-12-22 Added OTA Update Capability
    Added over-the-air updates so I can update without removing from the wall. Needs to be flashed manually (with USB cable) first, to enable the OTA update capability.
